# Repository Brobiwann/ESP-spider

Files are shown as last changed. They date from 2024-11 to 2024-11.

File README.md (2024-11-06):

# ESP-spider

The ESP-Spider is a quadruped robot inspired by the miniKame (https://github.com/JavierIH/miniKame) . Like the miniKame, it uses sinusoidal functions to control servo positions,
but the design and code were developed independently to better learn the process.
Currently, the robot performs three main actions: move forward, turn right, and turn left, with plans to add more functions in the future as I learn.
Robot and cad Inside robot

# Electronics

The robot features a custom PCB (gerber files and KiCad project are in the repository) with:

  - ESP32 module
  - PCA9685 for PWM control of servos
    
Additional components:

  - 8x MG92B servos
  - 3x 18650 cells
  - 3S BMS 40A 12V with balance charging
  - DFR0753 (DC-DC Buck Converter 6–14V to 5V/8A)
  - Adafruit 1.2" 8x8 LED Matrix Backpack
  - 2.1mmx5.5mm DC Power Jack (Female)
  - Mini 5V fan (20mmx10mm)

# 3D Printing

All STL, Soliworks and STEP files are provided in the repository.
The design is optimized for resin printing and also uses 4x 11mm ball bearings to support the robot weight.
The assembly is completed using M3 and M2 bolts and nuts

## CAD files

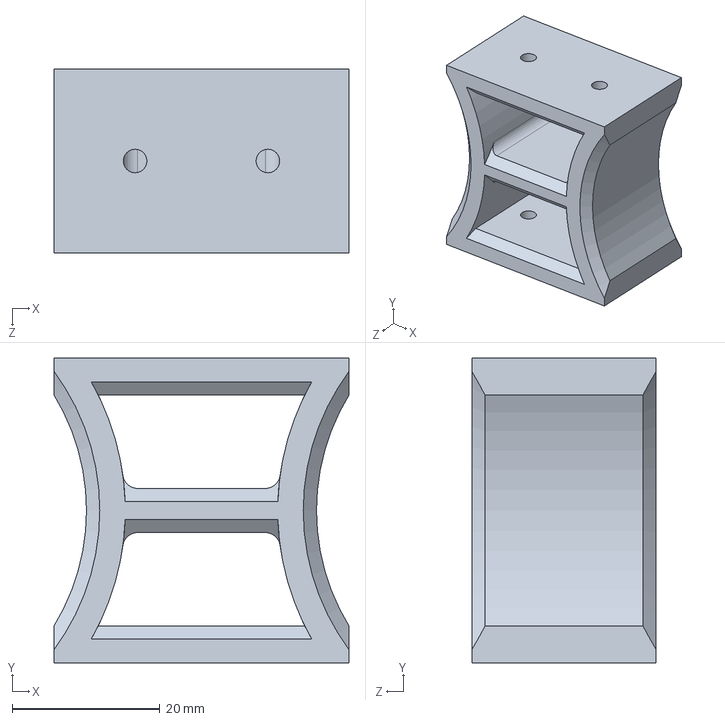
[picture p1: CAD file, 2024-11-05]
Solidworks/body/spacer main body.SLDPRT
40.0 x 41.3 x 25.0 mm

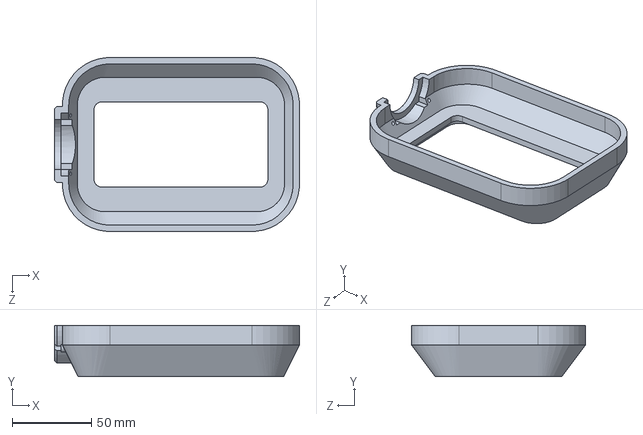
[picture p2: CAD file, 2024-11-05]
Solidworks/body/main body top.SLDPRT
155.0 x 32.5 x 110.0 mm

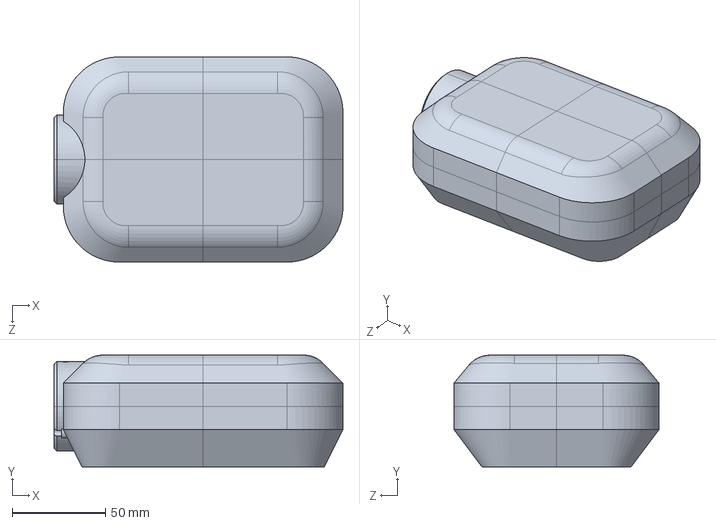
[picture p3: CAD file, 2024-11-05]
Solidworks/body/main body.SLDPRT
155.0 x 60.0 x 110.0 mm

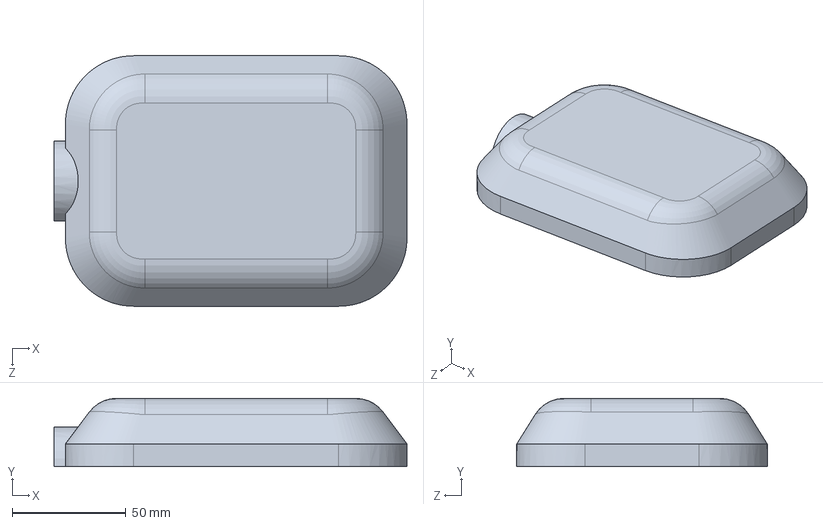
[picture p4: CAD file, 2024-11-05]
Solidworks/body/main body bottom.SLDPRT
155.0 x 30.0 x 110.0 mm

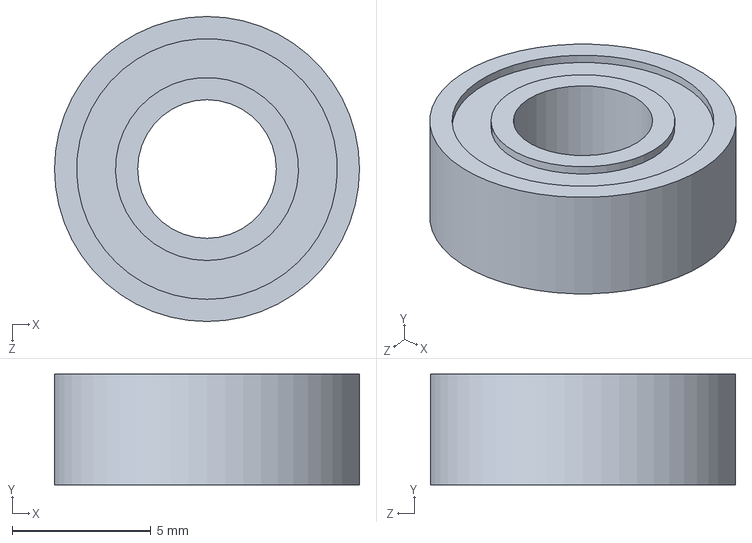
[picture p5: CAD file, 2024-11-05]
Solidworks/body/Bearing11mm.SLDPRT
11.0 x 4.00 x 11.0 mm

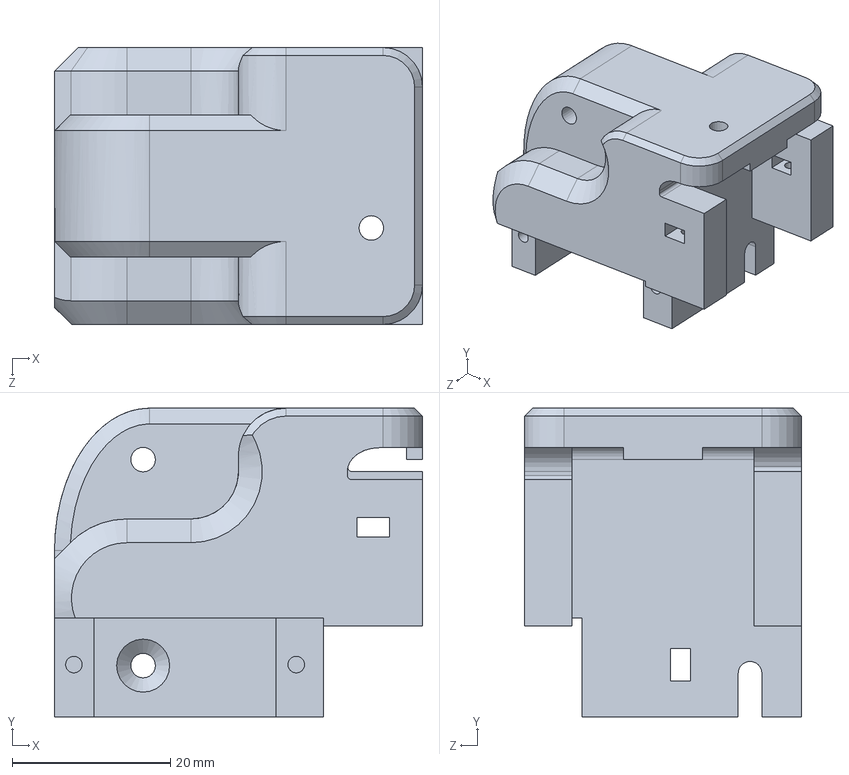
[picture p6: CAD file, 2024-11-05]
Solidworks/legs/leg servos support mirror.SLDPRT
46.5 x 39.0 x 35.0 mm

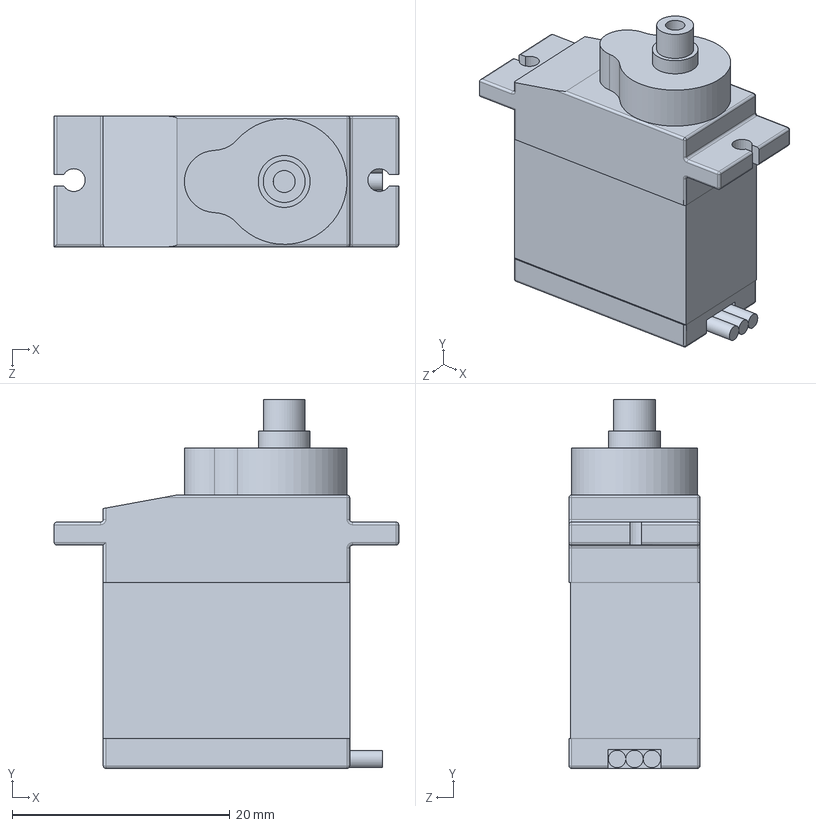
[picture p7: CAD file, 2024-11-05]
Solidworks/MG92B/SERVO MG92B.SLDPRT
31.7 x 33.9 x 12.1 mm

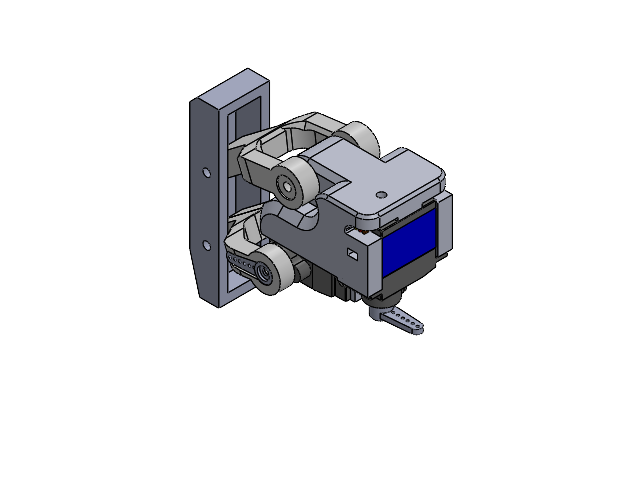
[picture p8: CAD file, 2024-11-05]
Solidworks/legs/leg assembly mirror.SLDASM
leg servos support mirror
SERVO MG92B x 2
bottom bar pin side mirror
bottom bar servo side mirror
Top bar leg
leg end
servo horn single x 2

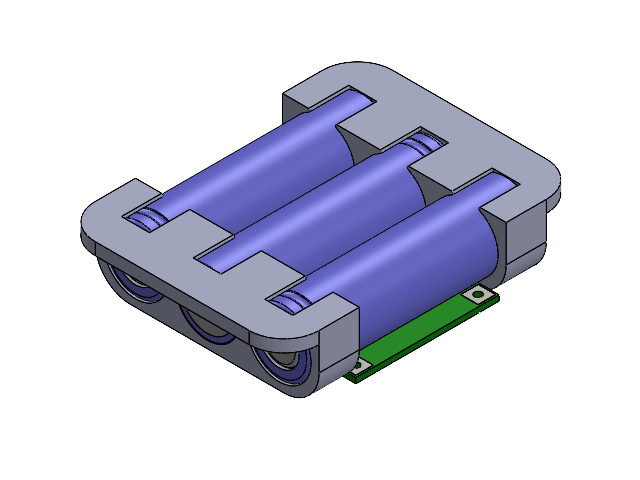
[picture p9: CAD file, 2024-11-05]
Solidworks/electronic/Battery pack.SLDASM
18650_Holder x 2
BMS 3S 40A.step

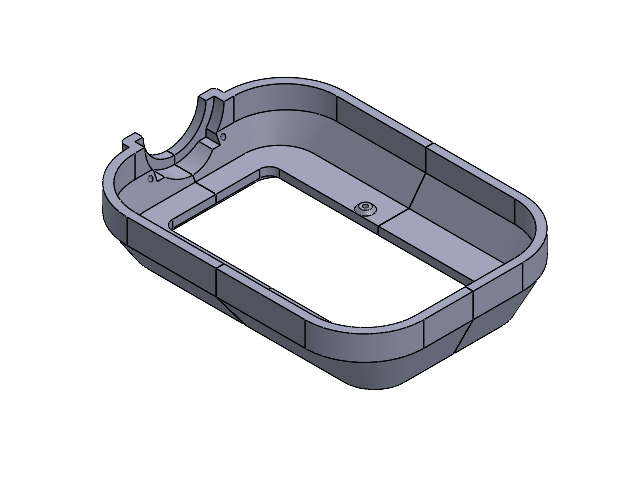
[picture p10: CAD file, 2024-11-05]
Solidworks/body/Body_Bottom.SLDASM
Body_Bottom_1
Body_Bottom_2
Body_Bottom_3
Body_Bottom_4

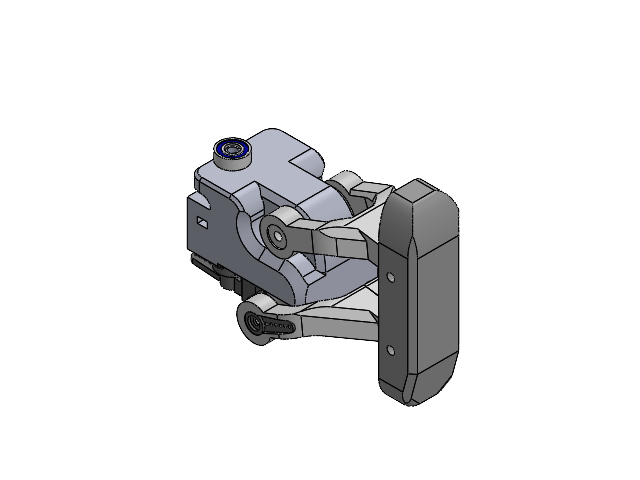
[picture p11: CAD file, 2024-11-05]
Solidworks/legs/leg assembly.SLDASM
leg servos support
SERVO MG92B x 2
Bottom bar leg
leg end
servo horn single x 2
bottom bar pin side
bottom bar servo side
Top bar leg
bearing plug
Bearing11mm

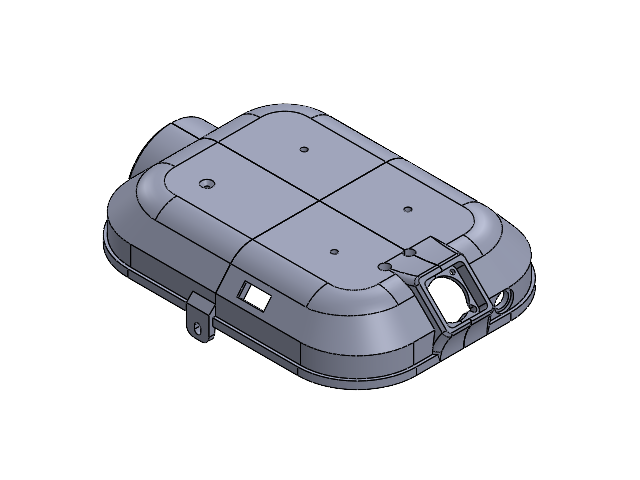
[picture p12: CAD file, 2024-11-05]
Solidworks/body/Body_Top.SLDASM
Body_Top_1
Body_Top_2
Body_Top_3
Body_Top_4
18650_Holder x 2
BMS 3S 40A.step

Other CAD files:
STEP/Spider assembly.STEP
STEP/leg assembly_1.STEP
STEP/leg assembly mirror_1.STEP
STEP/leg assembly mirror.STEP
STEP/leg assembly.STEP
STEP/spacer main body.STEP
STEP/18650.STEP
STEP/18650_Holder.STEP
STEP/2006_Fan.step.STEP
STEP/Battery pack.STEP
STEP/Bearing11mm.STEP
STEP/Body_Bottom.STEP
STEP/Body_Bottom_1.STEP
STEP/Body_Bottom_2.STEP
STEP/Body_Bottom_3.STEP
STEP/Body_Bottom_4.STEP
STEP/Body_Top.STEP
STEP/Body_Top_1.STEP
STEP/Body_Top_2.STEP
STEP/Body_Top_3.STEP
STEP/Body_Top_4.STEP
STEP/Bottom bar leg.STEP
STEP/Bottom body.STEP
STEP/Knob.STEP
STEP/Led Matrix.STEP
STEP/M3 Nyloc Nut.STEP
STEP/Pin1 (1).step.STEP
STEP/Pin1 (2).step.STEP
STEP/Pin1.step.STEP
STEP/Pin1_1.step.STEP
STEP/Pin2 (1).step.STEP
STEP/Pin2 (2).step.STEP
STEP/Pin2.step.STEP
STEP/Pin2_1.step.STEP
STEP/Power jack.STEP
STEP/Rubber plug.STEP
STEP/SERVO MG92B_Predeterminado.STEP
STEP/Top bar leg.STEP
STEP/Top body.STEP
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

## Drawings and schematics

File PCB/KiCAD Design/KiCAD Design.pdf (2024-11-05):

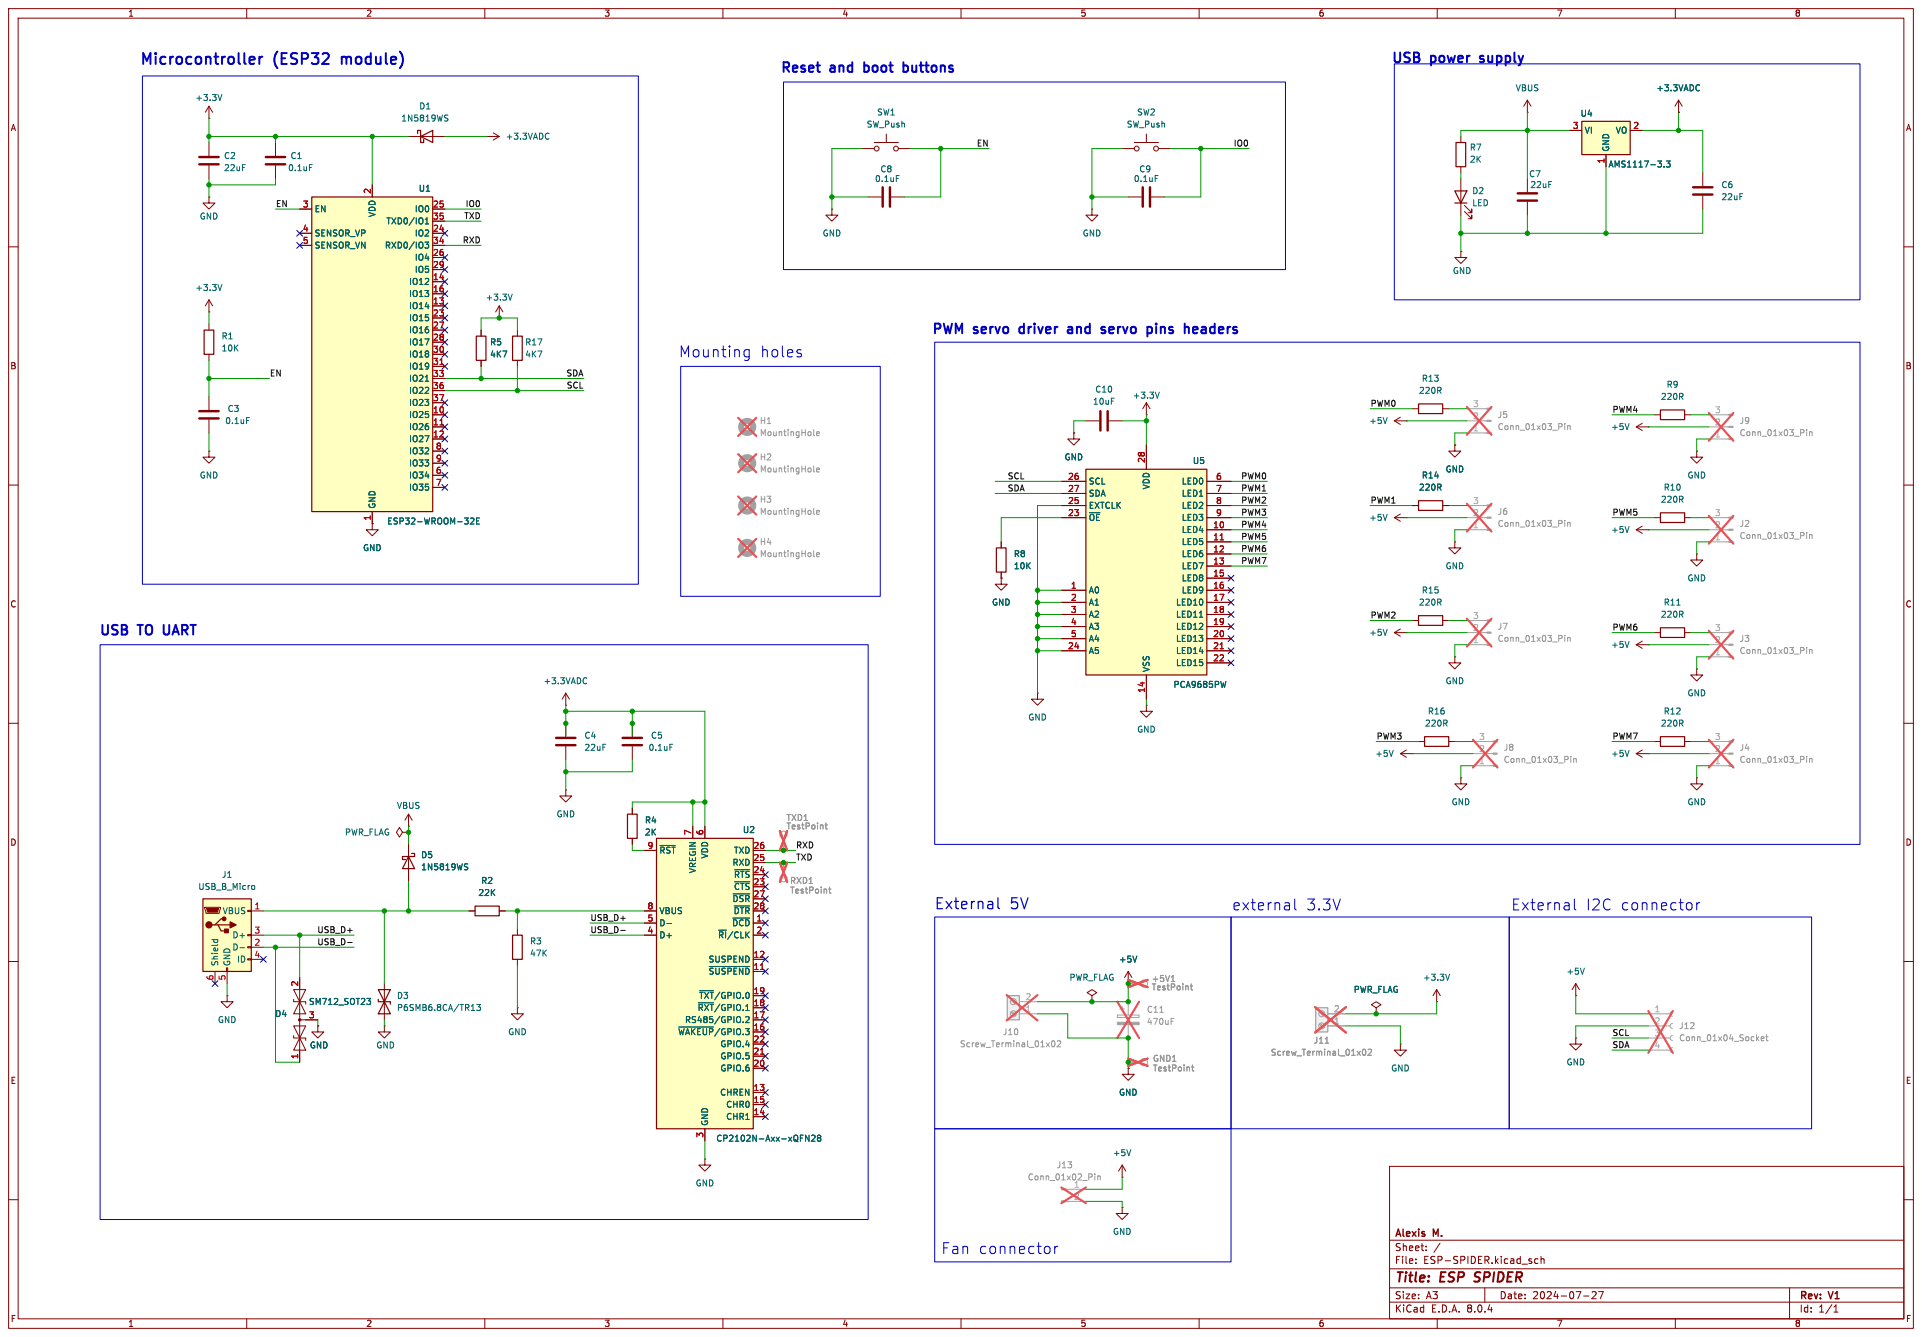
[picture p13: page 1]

PWM servo driver and servo pins headers

Id: 1/1 Title: ESP SPIDER

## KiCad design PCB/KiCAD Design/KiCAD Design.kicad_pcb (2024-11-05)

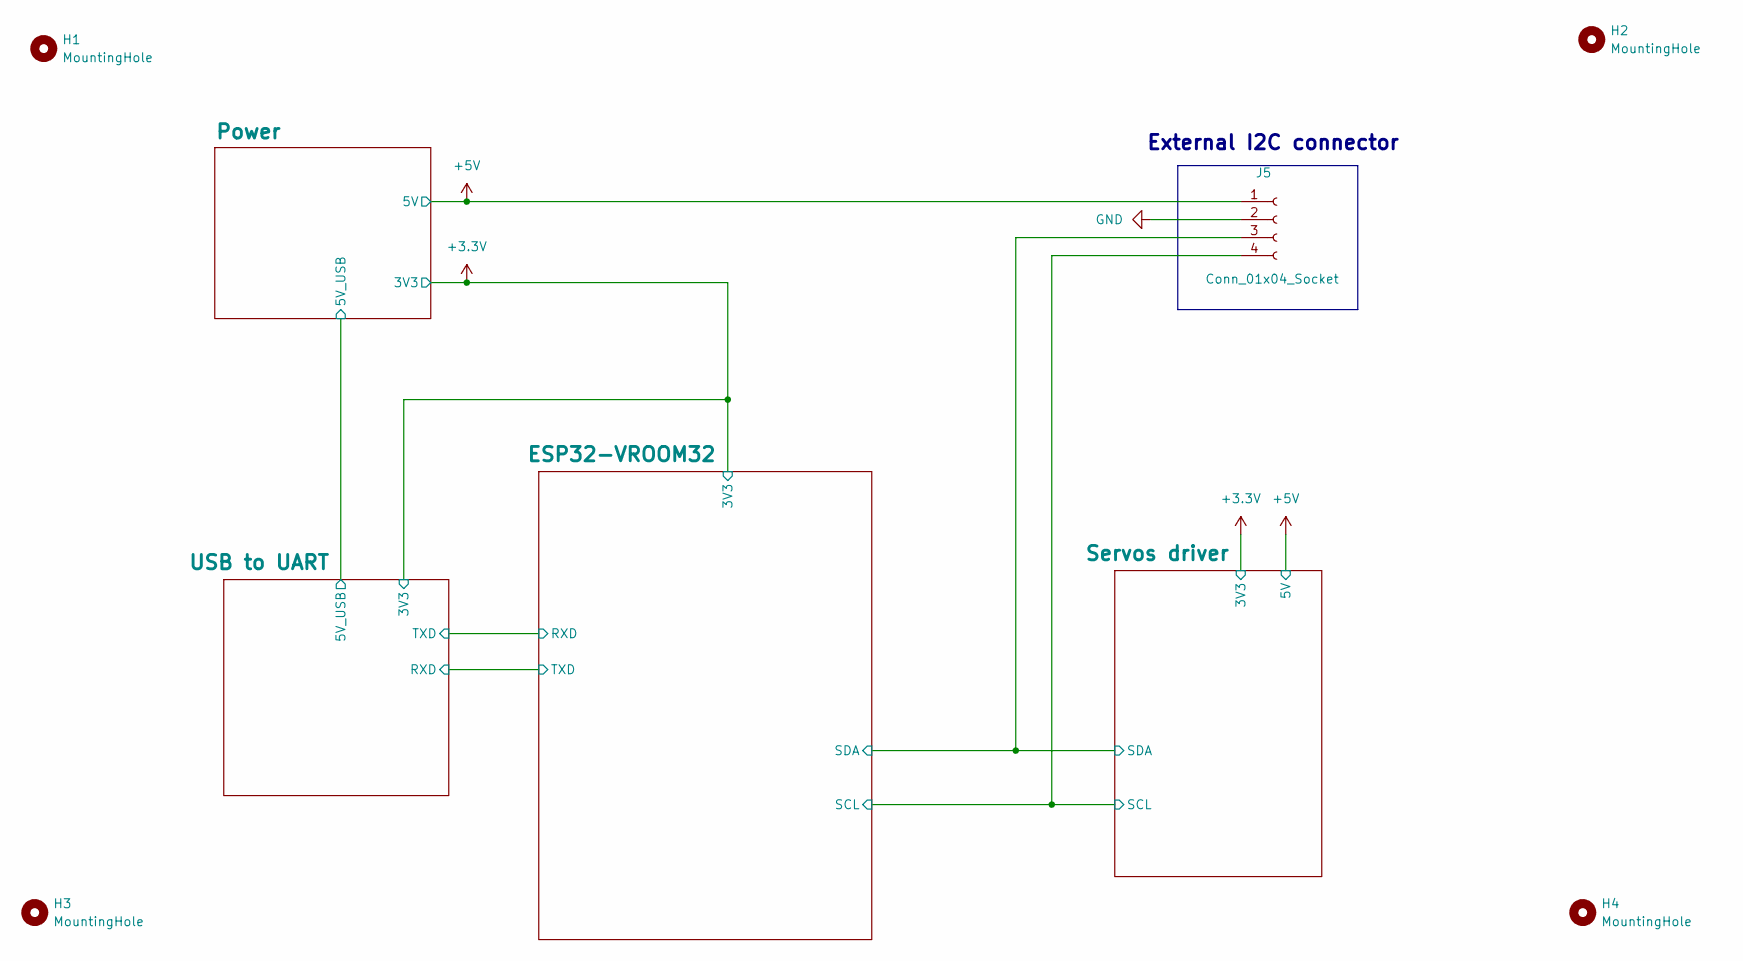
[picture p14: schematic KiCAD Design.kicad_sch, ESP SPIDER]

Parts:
H1, H2, H3, H4: MountingHole; MountingHole_2.2mm_M2
J5: Conn_01x04_Socket; JST_PH_B4B-PH-K_1x04_P2.00mm_Vertical; LCSC C131334

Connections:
+5V: J5.1; also elsewhere on the board
/ESP32-VROOM32/SCL: J5.4; also elsewhere on the board
/ESP32-VROOM32/SDA: J5.3; also elsewhere on the board
GND: J5.2; also elsewhere on the board

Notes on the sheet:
External I2C connector

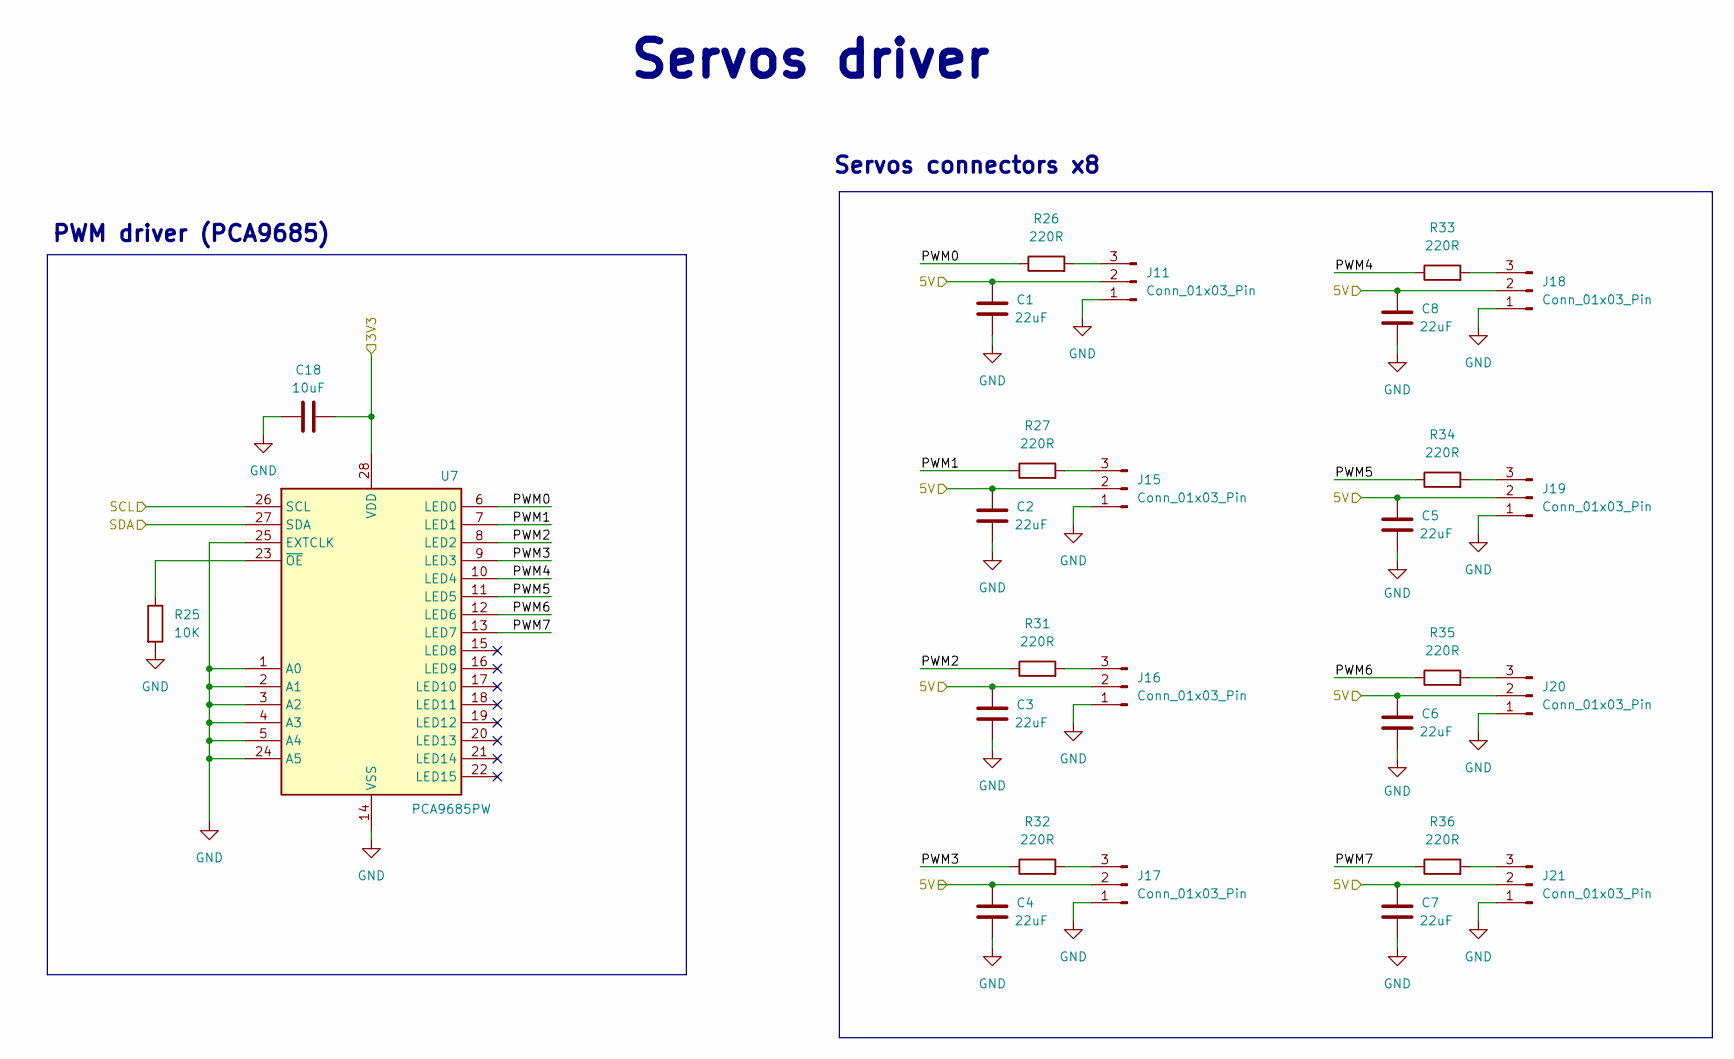
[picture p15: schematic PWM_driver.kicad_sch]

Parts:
C1, C2, C3, C4, C5, C6, C7, C8: 22uF; C_0603_1608Metric; LCSC C59461
C18: 10uF; C_0603_1608Metric_Pad1.08x0.95mm_HandSolder; LCSC C19702
J11, J15, J16, J17, J18, J19, J20, J21: Conn_01x03_Pin; PinHeader_1x03_P2.54mm_Vertical
R25: 10K; R_0603_1608Metric_Pad0.98x0.95mm_HandSolder; LCSC C25804
R26, R27, R31, R32, R33, R34, R35, R36: 220R; R_0603_1608Metric_Pad0.98x0.95mm_HandSolder; LCSC C22962
U7: PCA9685PW; TSSOP-28_4.4x9.7mm_P0.65mm; LCSC C2678753

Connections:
+3.3V: C18.1, U7.28 (VDD); also elsewhere on the board
+5V: C1.2, C2.2, C3.2, C4.2, C5.2, C6.2, C7.2, C8.2, J11.2, J15.2, J16.2, J17.2, J18.2, J19.2, J20.2, J21.2; also elsewhere on the board
/ESP32-VROOM32/SCL: U7.26 (SCL); also elsewhere on the board
/ESP32-VROOM32/SDA: U7.27 (SDA); also elsewhere on the board
/Servos driver/PWM0: R26.1, U7.6 (LED0)
/Servos driver/PWM1: R27.1, U7.7 (LED1)
/Servos driver/PWM2: R31.1, U7.8 (LED2)
/Servos driver/PWM3: R32.1, U7.9 (LED3)
/Servos driver/PWM4: R33.1, U7.10 (LED4)
/Servos driver/PWM5: R34.1, U7.11 (LED5)
/Servos driver/PWM6: R35.1, U7.12 (LED6)
/Servos driver/PWM7: R36.1, U7.13 (LED7)
GND: C1.1, C2.1, C3.1, C4.1, C5.1, C6.1, C7.1, C8.1, C18.2, J11.1, J15.1, J16.1, J17.1, J18.1, J19.1, J20.1, J21.1, R25.2, U7.1 (A0), U7.2 (A1), U7.3 (A2), U7.4 (A3), U7.5 (A4), U7.14 (VSS), U7.24 (A5), U7.25 (EXTCLK); also elsewhere on the board
unnamed: J11.3, R26.2
unnamed: J15.3, R27.2
unnamed: J16.3, R31.2
unnamed: J17.3, R32.2
unnamed: J18.3, R33.2
unnamed: J19.3, R34.2
unnamed: J20.3, R35.2
unnamed: J21.3, R36.2
unnamed: R25.1, U7.23 (~OE)

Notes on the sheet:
Servos driver
Servos connectors x8
PWM driver (PCA9685)

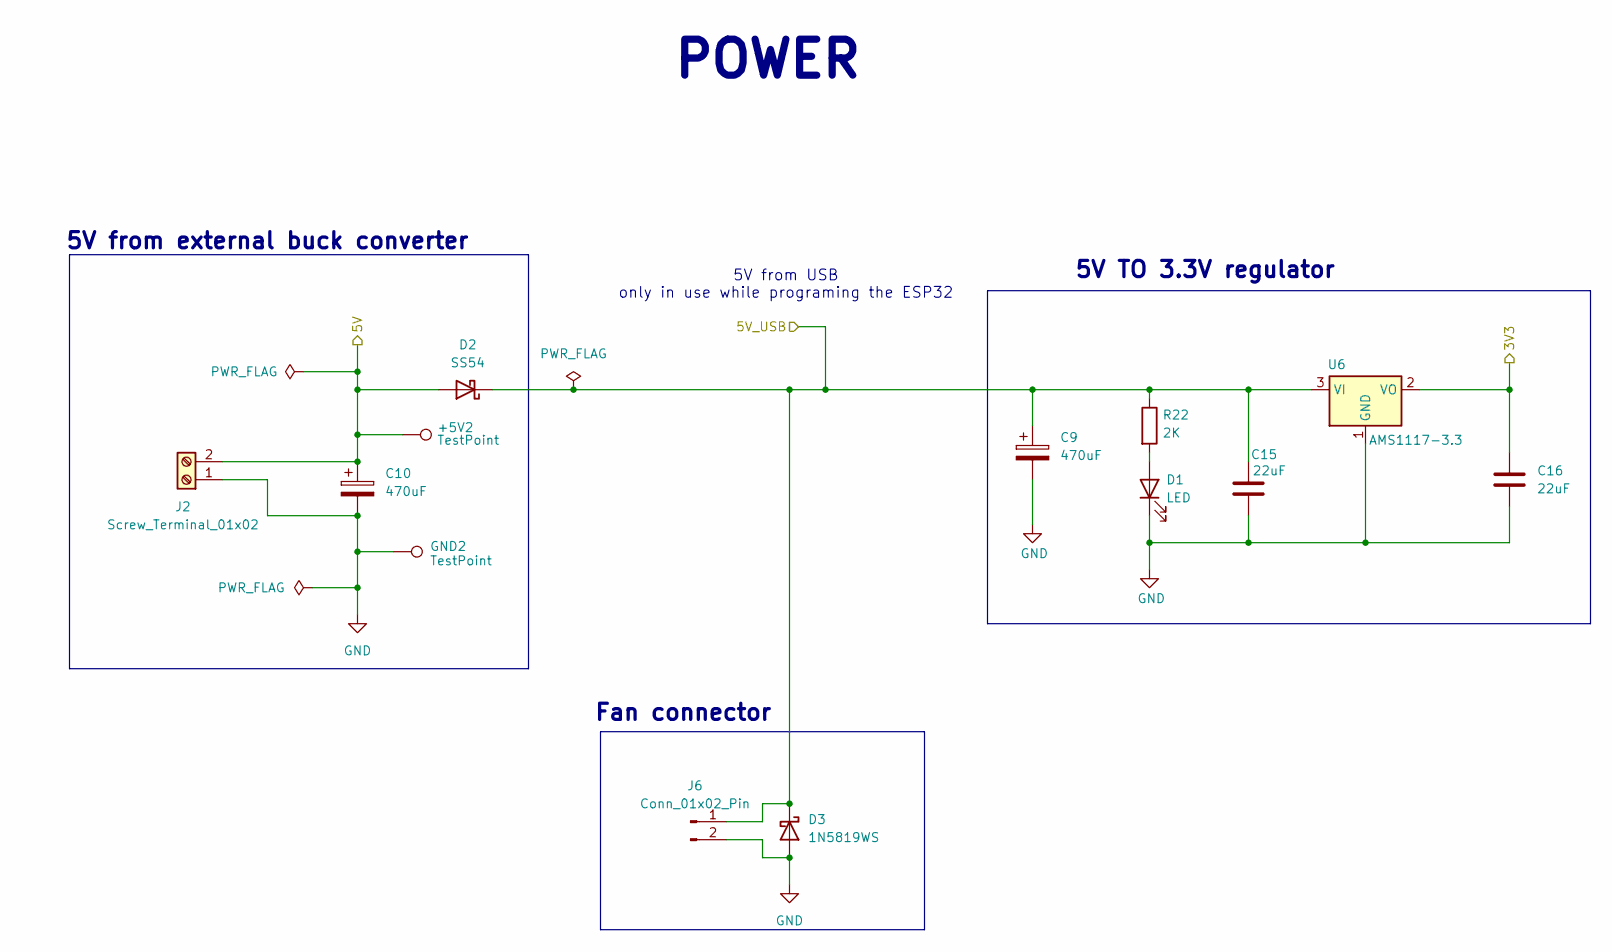
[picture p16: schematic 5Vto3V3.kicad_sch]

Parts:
+5V2: TestPoint; TestPoint_Pad_D1.5mm
C9, C10: 470uF; CP_Radial_D8.0mm_P3.50mm
C15, C16: 22uF; C_0603_1608Metric; LCSC C59461
D1: LED; LED_0603_1608Metric_Pad1.05x0.95mm_HandSolder; LCSC C2286
D2: SS54; D_SMA; LCSC C22452
D3: 1N5819WS; D_SOD-323; LCSC C191023
GND2: TestPoint; TestPoint_Pad_D1.5mm
J2: Screw_Terminal_01x02; TerminalBlock_Phoenix_PT-1,5-2-3.5-H_1x02_P3.50mm_Horizontal
J6: Conn_01x02_Pin; JST_PH_B2B-PH-K_1x02_P2.00mm_Vertical
R22: 2K; R_0603_1608Metric_Pad0.98x0.95mm_HandSolder; LCSC C22975
U6: AMS1117-3.3; SOT-223-3_TabPin2; LCSC C6186

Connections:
+3.3V: C16.1, U6.2 (VO); also elsewhere on the board
+5V: +5V2.1, C10.1, D2.2 (A), J2.2; also elsewhere on the board
/Power/5V_USB: C9.1, C15.1, D2.1 (K), D3.1 (K), J6.1, R22.1, U6.3 (VI); also elsewhere on the board
GND: C9.2, C10.2, C15.2, C16.2, D1.1 (K), D3.2 (A), GND2.1, J2.1, J6.2, U6.1 (GND); also elsewhere on the board
unnamed: D1.2 (A), R22.2

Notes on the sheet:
Fan connector
POWER
5V from USB only in use while programing the ESP32
5V from external buck converter
5V TO 3.3V regulator

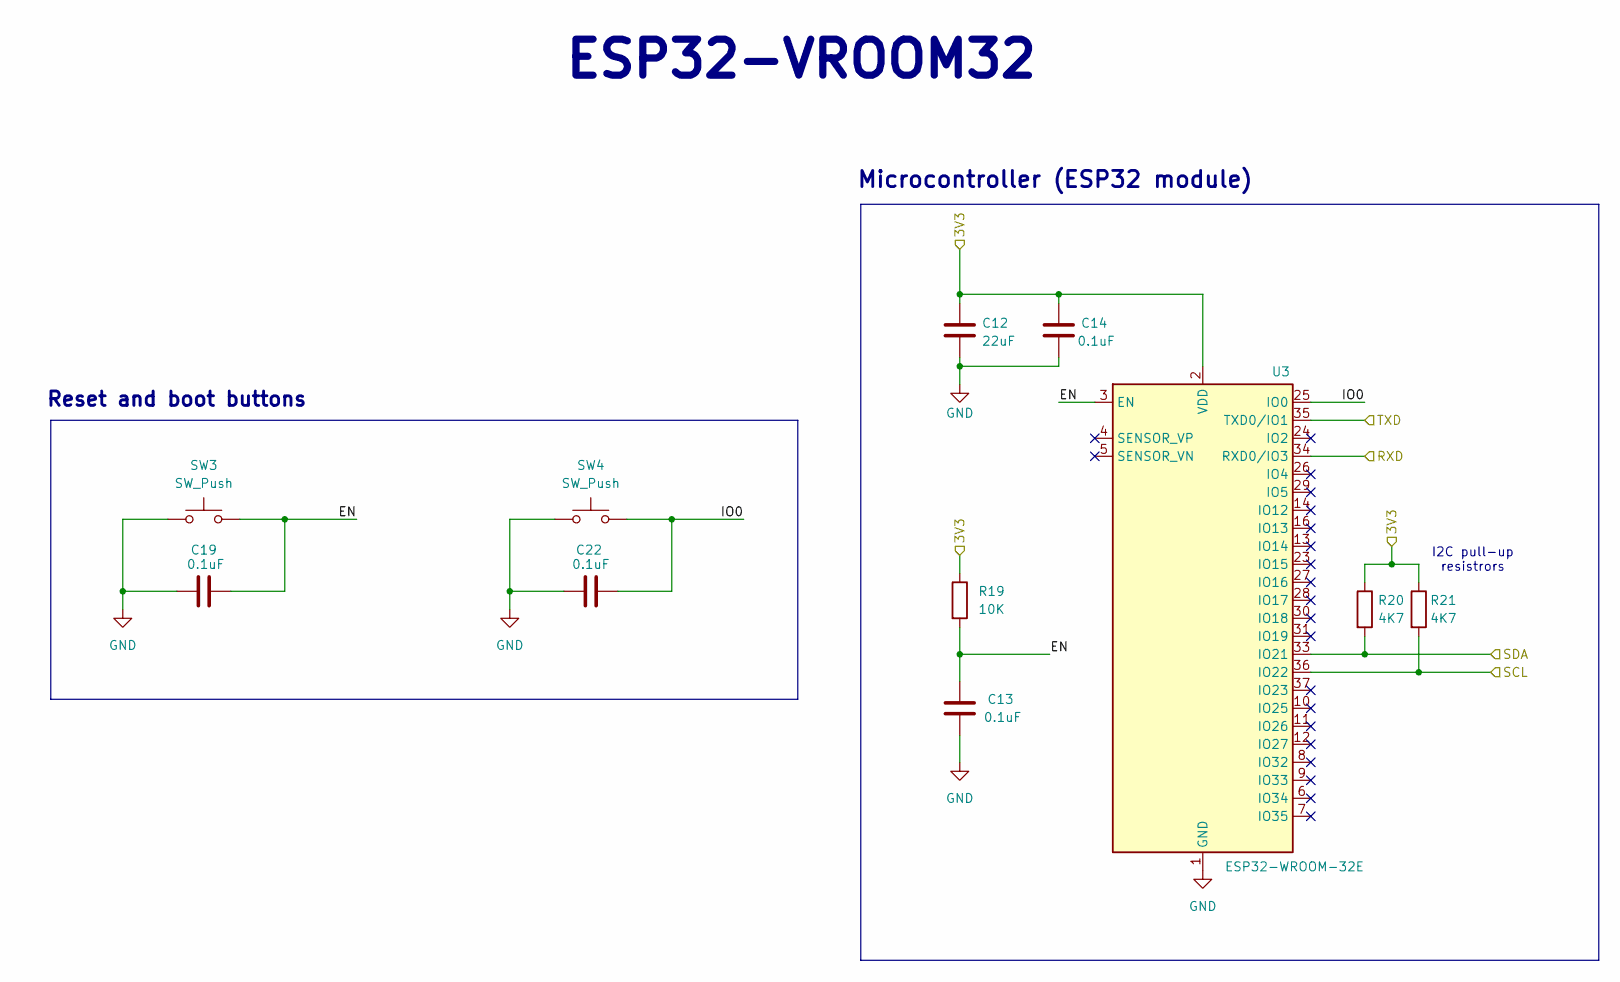
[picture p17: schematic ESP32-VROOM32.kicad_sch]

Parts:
C12: 22uF; C_0603_1608Metric; LCSC C59461
C13, C14, C19, C22: 0.1uF; C_0603_1608Metric_Pad1.08x0.95mm_HandSolder; LCSC C14663
R19: 10K; R_0603_1608Metric_Pad0.98x0.95mm_HandSolder; LCSC C25804
R20, R21: 4K7; R_0603_1608Metric_Pad0.98x0.95mm_HandSolder; LCSC C23162
SW3, SW4: SW_Push; SW_Push_1P1T_NO_6x6mm_H9.5mm; LCSC C255812
U3: ESP32-WROOM-32E; ESP32-WROOM-32D; LCSC C701342

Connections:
+3.3V: C12.1, C14.1, R19.1, R20.1, R21.1, U3.2 (VDD); also elsewhere on the board
/ESP32-VROOM32/EN: C13.1, C19.1, R19.2, SW3.2, U3.3 (EN)
/ESP32-VROOM32/IO0: C22.1, SW4.2, U3.25 (IO0)
/ESP32-VROOM32/RXD: U3.34 (RXD0/IO3); also elsewhere on the board
/ESP32-VROOM32/SCL: R21.2, U3.36 (IO22); also elsewhere on the board
/ESP32-VROOM32/SDA: R20.2, U3.33 (IO21); also elsewhere on the board
/ESP32-VROOM32/TXD: U3.35 (TXD0/IO1); also elsewhere on the board
GND: C12.2, C13.2, C14.2, C19.2, C22.2, SW3.1, SW4.1, U3.1 (GND), U3.15 (GND), U3.38 (GND), U3.39 (GND); also elsewhere on the board

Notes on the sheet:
Microcontroller (ESP32 module)
ESP32-VROOM32
Reset and boot buttons
I2C pull-up resistrors

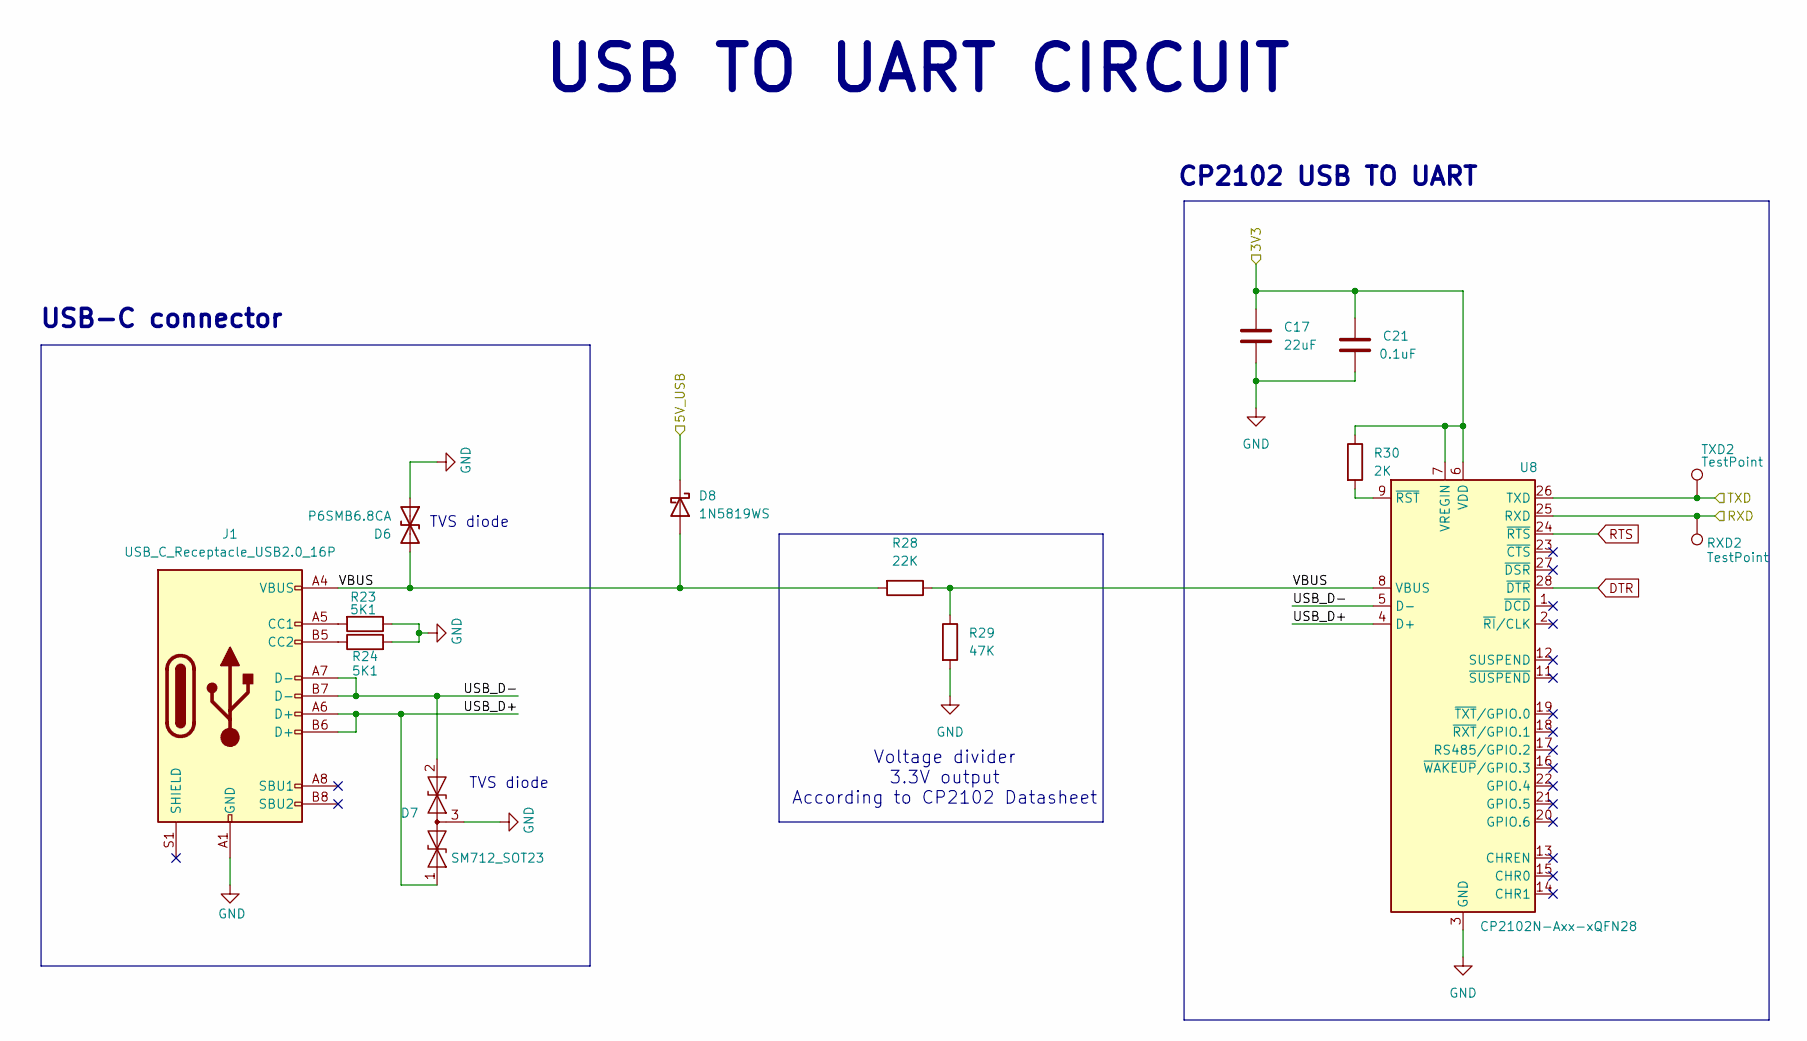
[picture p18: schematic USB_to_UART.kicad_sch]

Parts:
C17: 22uF; C_0603_1608Metric; LCSC C59461
C21: 0.1uF; C_0603_1608Metric_Pad1.08x0.95mm_HandSolder; LCSC C14663
D6: P6SMB6.8CA; D_SMB; LCSC C78395
D7: SM712_SOT23; SOT-23; LCSC C32677
D8: 1N5819WS; D_SOD-323; LCSC C191023
J1: USB_C_Receptacle_USB2.0_16P; USB_C_Receptacle_G-Switch_GT-USB-7010ASV; LCSC C2988369
R23, R24: 5K1; R_0603_1608Metric; LCSC C23186
R28: 22K; R_0603_1608Metric_Pad0.98x0.95mm_HandSolder; LCSC C31850
R29: 47K; R_0603_1608Metric_Pad0.98x0.95mm_HandSolder; LCSC C25819
R30: 2K; R_0603_1608Metric_Pad0.98x0.95mm_HandSolder; LCSC C22975
RXD2: TestPoint; TestPoint_Pad_D1.5mm
TXD2: TestPoint; TestPoint_Pad_D1.5mm
U8: CP2102N-Axx-xQFN28; QFN-28-1EP_5x5mm_P0.5mm_EP3.1x3.1mm; LCSC C6568

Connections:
+3.3V: C17.1, C21.1, R30.1, U8.6 (VDD), U8.7 (VREGIN); also elsewhere on the board
/ESP32-VROOM32/RXD: TXD2.1, U8.26 (TXD); also elsewhere on the board
/ESP32-VROOM32/TXD: RXD2.1, U8.25 (RXD); also elsewhere on the board
/Power/5V_USB: D8.1 (K); also elsewhere on the board
/USB to UART/USB_D+: D7.1 (A1), J1.A6 (D+), J1.B6 (D+), U8.4 (D+)
/USB to UART/USB_D-: D7.2 (A2), J1.A7 (D-), J1.B7 (D-), U8.5 (D-)
/USB to UART/VBUS: D6.2 (A2), D8.2 (A), J1.A4 (VBUS), J1.A9 (VBUS), J1.B4 (VBUS), J1.B9 (VBUS), R28.1, R28.2, R29.1, U8.8 (VBUS)
DTR: U8.28 (~DTR)
GND: C17.2, C21.2, D6.1 (A1), D7.3 (common), J1.A1 (GND), J1.A12 (GND), J1.B1 (GND), J1.B12 (GND), R23.1, R24.2, R29.2, U8.3 (GND), U8.29 (GND); also elsewhere on the board
unnamed: J1.A5 (CC1), R23.2
unnamed: J1.B5 (CC2), R24.1
unnamed: R30.2, U8.9 (~RST)
RTS: U8.24 (~RTS)

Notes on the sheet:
CP2102 USB TO UART
TVS diode
Voltage divider 3.3V output According to CP2102 Datasheet
USB TO UART CIRCUIT
USB-C connector

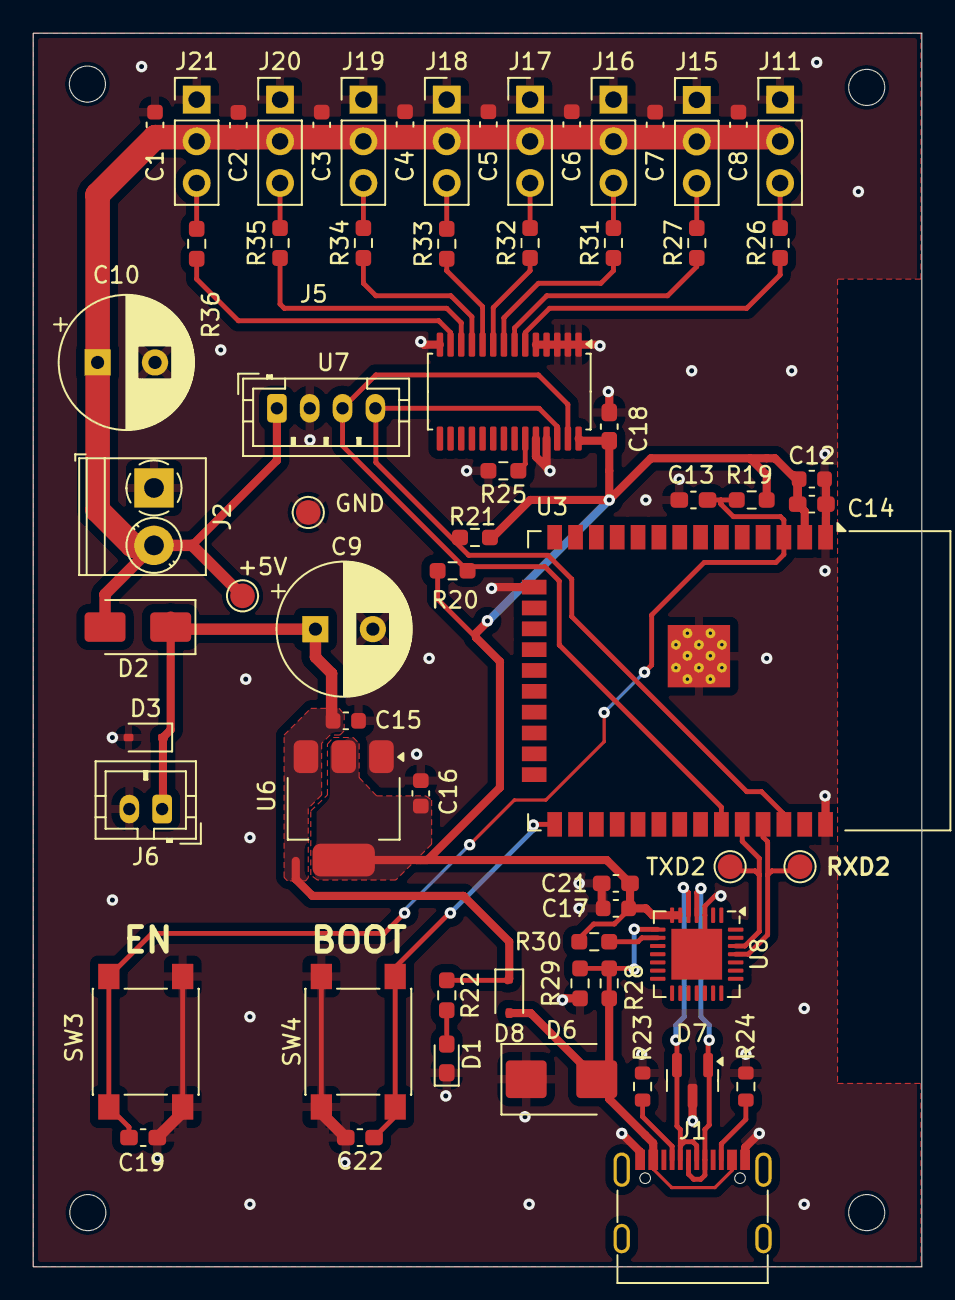
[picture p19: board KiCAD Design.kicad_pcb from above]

Board: 2 copper layers, 54.2 x 75.2 mm, 70 parts (0 on the bottom side), 34 nets.

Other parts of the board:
+5V: TestPoint; TestPoint_Pad_D1.5mm
GND: TestPoint; TestPoint_Pad_D1.5mm

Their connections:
+5V: +5V.1; also elsewhere on the board
GND: GND.1; also elsewhere on the board

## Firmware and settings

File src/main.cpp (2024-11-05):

//ESP-SPIDER
//The robot is a small 4 legged robot, two servos are used per leg
//The idea is inspired by the minikame by JavierIH https://github.com/JavierIH/miniKame
//
// This code enables the robot to walk in different directions using a PS4 controller. (Thanks to this amazing library : https://github.com/aed3/PS4-esp32)
// The robot's movement is controlled by eight servos (lift and rotation per leg) using a PCA9685 driver, 
// with each servo’s position updated through a sinusoidal function.
//
// The sinusoidal motion is calculated based on three parameters: amplitude, period, and phase offset, 
// which define the lift and rotation patterns for forward or turning movements. Each servo's pulse 
// width is adjusted to create smooth, cyclic motion, where the phase offset allows coordination 
// between servos for synchronized steps. 
//
// The eye of the robot is an Adafruit 8x8 LED Matrix w/I2C Backpack, it's also controlled by I2C
// The eye moves right and left when the robot turns, 
// And it's moving 1 pixel left and right in sync with the movement when the robot is going forward

#include <Arduino.h>
#include <Wire.h>
#include <SPI.h>
#include <Adafruit_PWMServoDriver.h>
#include <Adafruit_GFX.h>
#include <Adafruit_LEDBackpack.h>
#include <PS4Controller.h>


// called this way, it uses the default address 0x40
Adafruit_PWMServoDriver pwm = Adafruit_PWMServoDriver();
Adafruit_8x8matrix matrix = Adafruit_8x8matrix();

#define SERVOMIN  100 // This is the 'minimum' pulse length count (out of 4096)
#define SERVOMAX  460 // This is the 'maximum' pulse length count (out of 4096)
#define SERVO_FREQ 50 // Analog servos run at 50 Hz updates

#define PI 3.1415926535897932384626433832795


int eye_pos[2] = {3, 2}; // Initial eye position

uint8_t servo_channels[8] = {0, 1, 2, 3, 4, 5, 6, 7}; // define servos locations pins on the PCA9685

// positions of the servos on the robot :
//0 = back left lift
//1 = back left rotation
//2 = front left lift
//3 = front left rotation
//4 = front right lift
//5 = front right rotation
//6 = back right lift
//7 = back right rotation

uint16_t initial_positions[8] = {265, 260, 295, 310, 250, 250, 300, 300};

float period_rota = 0.6;
float period_lift = period_rota/2;


float phase_offset[8];
float period[8];
int amplitude[8];


uint16_t current_pwm_value = 0;
uint16_t previous_pwm_values[8];




// Function to calculate the next pulse width of each servo.
uint16_t calculate_servo_pulse(float period, float amplitude, float phase, int initial_pos) {

  float time_elapsed = millis() / 1000.0;

  // Getting the frequency using the period (the period is the time for a full movement of a servo)
  float frequency = (2 * PI) / period;
  
  //creating the sinusoidal function
  float pulse_width = amplitude * sin(frequency * time_elapsed + phase) + initial_pos;

return pulse_width;
}




//Function to set the parameters of the sinusoidal function for the robot to go forward
void Set_Parameters_Up() {

  float Up_phase_offset[8] = {PI+PI/2, 0, PI/2, PI, PI+PI/2 , PI, PI/2, 0};
  float Up_period[8] = {period_lift, period_rota, period_lift, period_rota, period_lift, period_rota, period_lift, period_rota};
  int Up_amplitude[8] = {27, 38, 27, 35, 27, 35, 27, 35};

  for (int i = 0; i < 8; i++) {
    phase_offset[i] = Up_phase_offset[i];
    period[i] = Up_period[i];
    amplitude[i] = Up_amplitude[i];
  }
}

//Function to set the parameters of the sinusoidal function for the robot to go right or left
//The parameters of the function are the same when the robot turn right or left
//In the main loop we just change the code so the legs stay in contact with the floor when the leg is turning clockwise or counter-clockwise
void Set_Parameters_Rotation() {

  float rotation_phase_offset[8] = {PI+PI/2, 0, PI/2, PI, PI+PI/2 , 0, PI/2, PI};
  float rotation_period[8] = {period_lift, period_rota, period_lift, period_rota, period_lift, period_rota, period_lift, period_rota};
  int rotation_amplitude[8] = {30, 25, 30, 25, 30, 25, 30, 25};

  for (int i = 0; i < 8; i++) {
    phase_offset[i] = rotation_phase_offset[i];
    period[i] = rotation_period[i];
    amplitude[i] = rotation_amplitude[i];
  }
}




void MoveEyeRight() {
  matrix.clear();
  matrix.drawRect(eye_pos[0] - 2, eye_pos[1], 2, 4, LED_ON);
  matrix.writeDisplay();
}

void MoveEyeLeft() {
  matrix.clear();
  matrix.drawRect(eye_pos[0] + 2, eye_pos[1], 2, 4, LED_ON);
  matrix.writeDisplay();
}

void MoveEyeCenter() {
  matrix.clear();
  matrix.drawRect(eye_pos[0],eye_pos[1], 2, 4, LED_ON);
  matrix.writeDisplay();
}

//Function to make the eye move right and left when the robot is walking
//The movement of the eye is linked to the movement of the back left rotation servo
void MoveEyeWalking(int i) {
  if (i==1) {
    if (current_pwm_value<previous_pwm_values[1]) {                            //Check if the leg is going CCW
      matrix.clear();                                                          //if so, clear matrix
      matrix.drawRect(eye_pos[0]+1,eye_pos[1], 2, 4, LED_ON);                  //move the eye to the left
      matrix.writeDisplay();                                                   //update led matrix display
    }            

    else if (current_pwm_value>previous_pwm_values[1]) {                       //Check if the leg is going CW
      matrix.clear();                                                          //if so, clear matrix
      matrix.drawRect(eye_pos[0]-1,eye_pos[1], 2, 4, LED_ON);                  //move the eye to the right
      matrix.writeDisplay();                                                   //update led matrix display
    }
  }
}





void setup() {

  Serial.begin(115200);
  matrix.begin(0x70);
  PS4.begin("e4:65:e8:75:7b:44"); //MAC address of the PS4 controller
  Serial.println("Ready.");

  pwm.begin();
  pwm.setOscillatorFrequency(27000000); // Setting the oscillator to match the clock of the PCA9685
  pwm.setPWMFreq(SERVO_FREQ);  // Analog servos run at ~50 Hz updates
  delay(10);

// Moving servos to initial positions
  for (int i = 0; i < 8; i++) {
    pwm.setPWM(servo_channels[i], 0, initial_positions[i]);
    delay(20);
  }
  delay(500); // Ensure servos have time to reach initial positions

}




void loop() {

  unsigned long currentMillis = millis();  // Track current time

  if (PS4.isConnected()) {

    if (PS4.Up()) {

      Serial.println("Up");
     
      Set_Parameters_Up(); // Set the offsets, amplitude, period for the robot to go forward

      for (int i = 0; i < 8; i++) {

        current_pwm_value = calculate_servo_pulse(period[i], amplitude[i], phase_offset[i], initial_positions[i]);

        MoveEyeWalking(i);

        //When going forward, for the lift servos 0 and 2,
        //we want those legs to stay in contact with the floor when the legs are turning CCW
        //So we get the the value of the rotation servo on the same leg
        //And we only update the servo if the leg is going CW
        if (i==0 || i==2) {
          uint16_t pwm_rotation = calculate_servo_pulse(period[i+1], amplitude[i+1], phase_offset[i+1], initial_positions[i+1]);
          if (pwm_rotation<previous_pwm_values[i+1]){
            pwm.setPWM(servo_channels[i], 0, current_pwm_value);      
          }
        }

        //When going forward, for the lift servos 4 and 6,
        //we want those legs to stay in contact with the floor when the legs are turning CW
        //So we get the the value of the rotation servo on the same leg
        //And we only update the servo if the leg is going CCW
        else if (i==4 || i==6) {
          uint16_t pwm_rotation = calculate_servo_pulse(period[i+1], amplitude[i+1], phase_offset[i+1], initial_positions[i+1]);
          if (pwm_rotation>previous_pwm_values[i+1]){
            pwm.setPWM(servo_channels[i], 0, current_pwm_value);    
          }     
        }
       
        else {pwm.setPWM(servo_channels[i], 0, current_pwm_value);}

        previous_pwm_values[i] = current_pwm_value;

      }
    }



    if (PS4.Right()) {

      Serial.println("Right");

      MoveEyeRight();

      Set_Parameters_Rotation(); // Set the offsets, amplitude, period for the robot to go Right

     for (int i = 0; i < 8; i++) {
        uint16_t current_pwm_value = calculate_servo_pulse(period[i], amplitude[i], phase_offset[i], initial_positions[i]);

        if (i==0 || i==2) {

          uint16_t pwm_rotation = calculate_servo_pulse(period[i+1], amplitude[i+1], phase_offset[i+1], initial_positions[i+1]);
          if (pwm_rotation<previous_pwm_values[i+1]){
            pwm.setPWM(servo_channels[i], 0, current_pwm_value);        
          }
        }

        
        else if (i==4 || i==6) {

          uint16_t pwm_rotation = calculate_servo_pulse(period[i+1], amplitude[i+1], phase_offset[i+1], initial_positions[i+1]);
          if (pwm_rotation<previous_pwm_values[i+1]){
            pwm.setPWM(servo_channels[i], 0, current_pwm_value);        
          }
        }
    
        else {pwm.setPWM(servo_channels[i], 0, current_pwm_value);}

        previous_pwm_values[i] = current_pwm_value;

      }
    }



    if (PS4.Left()) {

      Serial.println("Left");

      MoveEyeLeft();

      Set_Parameters_Rotation(); // Set the offsets, amplitude, period for the robot to go left

     for (int i = 0; i < 8; i++) {
        uint16_t current_pwm_value = calculate_servo_pulse(period[i], amplitude[i], phase_offset[i], initial_positions[i]);

        if (i==0 || i==2) {

          uint16_t pwm_rotation = calculate_servo_pulse(period[i+1], amplitude[i+1], phase_offset[i+1], initial_positions[i+1]);
          if (pwm_rotation>previous_pwm_values[i+1]){
            pwm.setPWM(servo_channels[i], 0, current_pwm_value);        
          }
        }

        
        else if (i==4 || i==6) {

          uint16_t pwm_rotation = calculate_servo_pulse(period[i+1], amplitude[i+1], phase_offset[i+1], initial_positions[i+1]);
          if (pwm_rotation>previous_pwm_values[i+1]){
            pwm.setPWM(servo_channels[i], 0, current_pwm_value);        
          }
        }

          
        else {pwm.setPWM(servo_channels[i], 0, current_pwm_value);}

        previous_pwm_values[i] = current_pwm_value;

      }
    }

    //if no button is press, move the eye in the center
    //and mlove the servos to initial positions
    if(!PS4.data.button.up && !PS4.data.button.right && !PS4.data.button.left) {

      MoveEyeCenter();

     for (int i = 0; i < 8; i++) {
       pwm.setPWM(servo_channels[i], 0, initial_positions[i]);
     }

     delay(20);

    }
  }
}
